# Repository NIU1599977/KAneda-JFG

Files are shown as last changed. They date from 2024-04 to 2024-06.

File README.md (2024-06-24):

# KAneda-JFG

Motocicleta auto-balanceable capaz de reconocer señales de tráfico mediante visión por computador.

## Tabla de Contenidos

+ [Descripción del Proyecto](#descripción-del-proyecto)
+ [Librerías y Configuración](#librerías-y-configuración)
+ [Componentes Electrónicos](#componentes-electrónicos)
+ [Componentes Mecánicos](#componentes-mecánicos)
+ [Esquema Eléctrico](#esquema-eléctrico)
+ [Diseño 3D](#diseño-3d)
+ [Arquitectura del Software](#arquitectura-del-software)
+ [Algorítmica](#algorítmica)
+ [Visión por Computador](#visión-por-computador)
+ [Simulación](#simulación)
+ [Contribuciones y Agradecimientos](#contribuciones-y-agradecimientos)
+ [Autoría](#autoría)
+ [Bibliografía](#bibliografía)

## Descripción del Proyecto

Este proyecto de motocicleta auto-balanceable surge con la visión de desarrollar un vehículo autónomo capaz de detectar y obedecer las señales de tráfico sin la intervención de un conductor. El propósito principal es brindar a la Dirección General de Tráfico (DGT) una herramienta para llevar a cabo demostraciones y programas educativos sobre seguridad vial. Utilizando técnicas avanzadas de visión por computador, nuestra moto puede interpretar y responder de manera precisa a las señales del entorno, lo que la convierte en un prototipo innovador en el campo de la movilidad autónoma.

La tecnología de auto-balanceo de la motocicleta se basa en el proyecto [Self-Balancing-Bike](https://github.com/remrc/Self-Balancing-Bike), realizado por [remrc](https://github.com/remrc) en Arduino.

## Librerías y Configuración

### Instalar Dependencias

1. Instalar git: `sudp apt install git`
2. Instalar gestor de librerías de python: `sudo apt install python3-pip`
3. Instalar librería smbus: `sudo apt install python3-smbus`
4. Instalar librería gpiozero: `sudo apt install python3-gpiozero`
5. Instalar librería mpu6050: `pip3 install mpu6050-raspberrypi`
6. Instalar librería numpy: `sudo apt install python3-numpy`
7. Instalar librería filterpy: `pip3 install filterpy`
8. Instalar librería openblas: `sudo apt install libopenblas-dev`
9. Instalar librería OpenCV: `sudo apt install python3-opencv`
10. Instalar librería PiCamera: `sudo apt install python3-picamera2`
11. Instalar Flask: `pip3 install flask`

\*Es posible que en ocasiones haya que añadir el parámetro `--break-system-packages` a los comandos `pip3 install <package>`.

### Activar Interfaces de Comunicación Hardware

1. Entrar en el asistente de configuración de la Raspberry: `sudo raspi-config`
2. Abrir _Interfacing Options_.
3. Activar cámara (_Enable Camera_).
4. Activar I2C.
5. Abrir _Advanced Options_.
6. Clicar _Expand Filesystem_.

### Activar el Demonio de PiGPIO

1. `sudo systemctl enable pigpiod`
2. `sudo pigpiod`

## Componentes Electrónicos

| Componente | Imagen | Componente | Imagen |
| --- | --- | --- | --- |
| [Kit Raspberry Pi Zero W + MicroSD 32GB](https://tienda.bricogeek.com/placas-raspberry-pi/1082-kit-basico-raspberry-pi-zero-wifi-microsd-32gb.html) |  | [Cámara Raspberry Pi v2 - 8 Megapíxeles](https://tienda.bricogeek.com/accesorios-raspberry-pi/822-camara-raspberry-pi-v2-8-megapixels.html) |  |
| [Cable cámara Raspberry Pi Zero (30cm)](https://tienda.bricogeek.com/accesorios-raspberry-pi/1562-cable-camara-raspberry-pi-zero-30cm.html) |  | [Módulo GY-521 Acelerómetro y Giroscopio MPU-6050](https://tienda.bricogeek.com/acelerometros/1682-modulo-gy-521-acelerometro-y-giroscopio-mpu-6050.html) |  |
| [Servo estándar S3003, 360 Grados](https://tienda.bricogeek.com/motores/118-servomotor-de-rotacion-continua-s3003-360-grados.html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) |  | [Motor paso a paso 28BYJ-48 (5V) con driver ULN2003](https://tienda.bricogeek.com/motores-paso-a-paso/969-motor-paso-a-paso-28byj-48-5v-con-driver-uln2003.html) |  |
| [Motor micro metal 75:1 HP con eje extendido](https://tienda.bricogeek.com/motores-dc/803-motor-micro-metal-751-hp-con-eje-extendido.html) |  | [BTS7960 Driver motor 43A de alta potencia](https://tienda.bricogeek.com/controladores-motores/1560-bts7960-driver-motor-43a-de-alta-potencia.html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) |  |
| [Bateria Lipo 1000mAh / 3.7V - 603050](https://tienda.bricogeek.com/baterias-lipo/135-bateria-lipo-1000mah-603050-37v.html) |  | [Cargador LiPo PowerBoost 500](https://tienda.bricogeek.com/convertidores-de-voltaje/677-cargador-lipo-powerboost-500.html) |  |

## Componentes Mecánicos

### Movimiento

| Componente | Imagen | Unidades |
| --- | --- | --- |
| [Rueda Solarbotics antideslizante](https://tienda.bricogeek.com/robotica/230-rueda-solarbotics-antideslizante.html) |  | 2 |
| [Rodamiento 608-2RS (8x22x7mm)](https://tienda.bricogeek.com/rodamientos/1294-rodamiento-608-2rs-8x22x7mm.html) |  | 2 |

### Tornillos

| Métrica | Longitud (cm) | Partes | Unidades | Tuercas |
| --- | --- | --- | --- | --- |
| M1 | 1 | Soporte Motor - Motor | 2 | Sí |
| M2 | 1 | Cámara | 2 | Sí |
| M2 | 2 | Servo | 2 | Sí |
| M3 | 1 | Soporte Stepper | 2 | Sí |
| M3 | 1,5 | Manillar, Frontal - Base, Base - Motor, Soporte Motor - Soporte Motor, Soporte Motor - Soporte Motor, Soporte Motor - Base | 12 | Sí |
| M3 | 2 | Culo | 4 | Sí |
| M3 | 3 | Base - Base | 2 | Sí |
| M4 | 0,5 | Volante de Inercia | 16 | Sí |

## Esquema Eléctrico

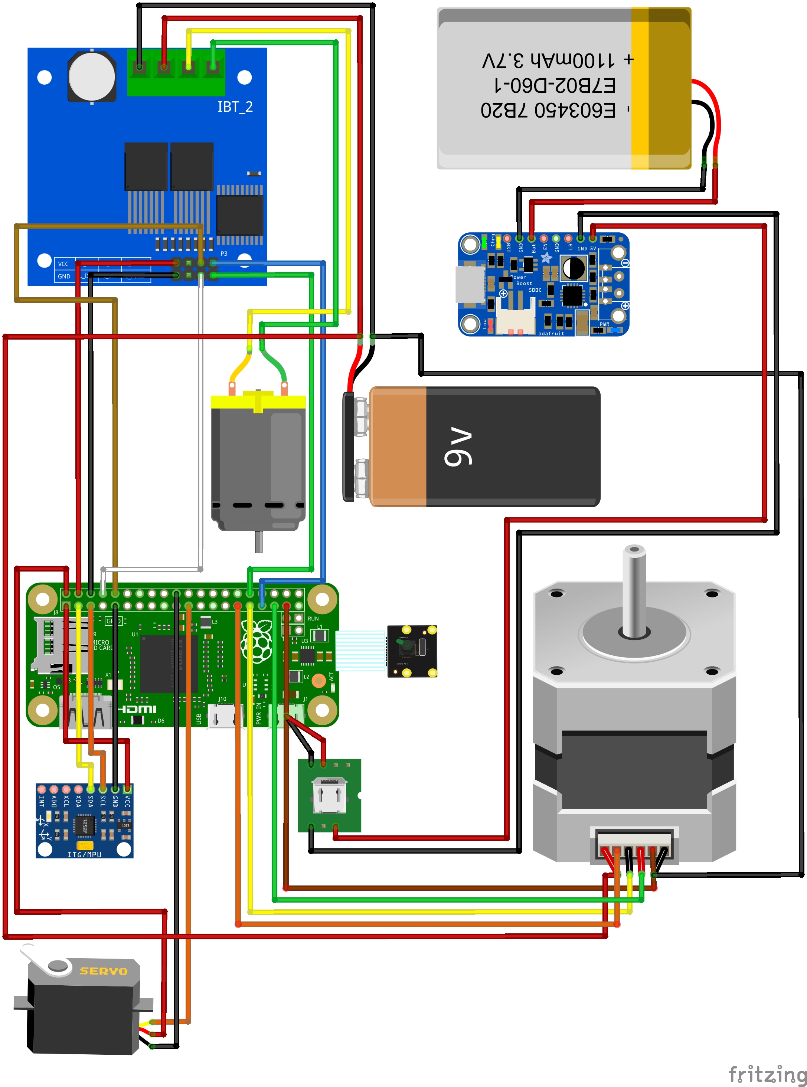
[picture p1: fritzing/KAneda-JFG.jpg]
KAneda-JFG


## Diseño 3D

Para el diseño 3D se ha optado por emplear los softwares FreeCAD y Cinema4D debido a que uno de los integrantes ya estaba familiarizado con él. El esqueleto de la motocicleta ha venido dado por el proyecto realizado por remrc, el cual tiene compartido en la página Thingiverse los [modelos](https://www.thingiverse.com/thing:5887157/files) que ha utilizado.

Estos modelos se han modificado para adecuarlos a nuestros componentes y de esta manera no exceder el presupuesto proporcionado por el profesorado. Los modelos han sido modificados de la siguiente manera.

### Manillar

Para el manillar, se ha utilizado el micro-servo SG90, por ello, ha sido necesario adaptar la pieza donde se asienta este componente.

| Antes | Después |
| --- | --- |
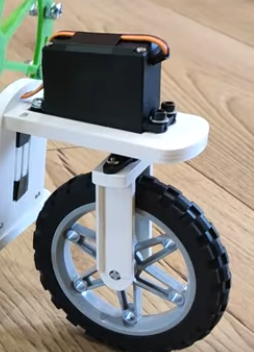
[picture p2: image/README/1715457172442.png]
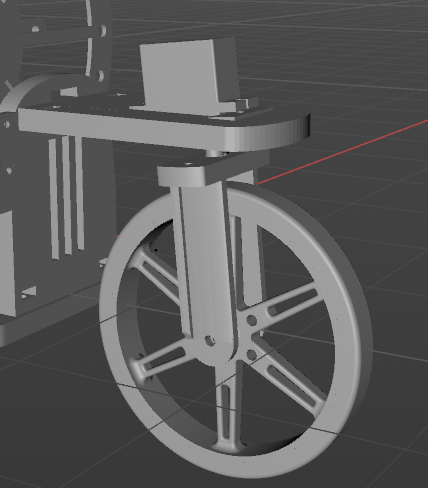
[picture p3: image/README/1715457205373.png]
|  |  |

### Volante de inercia

El volante de inercia es el alma de esta motocicleta, por tanto su diseño se ha intentado mantener con respecto al utilizado por remrc. En nuestro caso, hemos adaptado el eje de adhesión para asegurar la compatibilidad con nuestro motor pololu.

| Antes | Después |
| --- | --- |
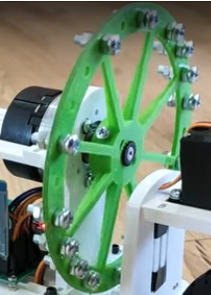
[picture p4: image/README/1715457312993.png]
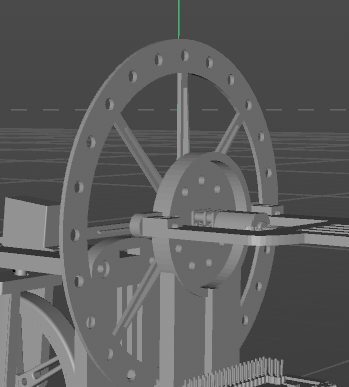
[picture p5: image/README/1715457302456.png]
|  |  |

### Cámara RPi

La motocicleta tiene soporte para utilizar visión por computador, por ello, se ha modificado la pieza que une al manillar con el cuerpo central de la motocicleta. La cámara se situaría en un lateral, esto es debido a que si se situase al frente del vehiculo, el cable no sería suficiente para llegar hasta el cuerpo central. La visión se vería ligeramente mermada a un lado por el propio manillar y la rueda delantera pero no debería suponer ningún problema.

| Antes | Después |
| --- | --- |
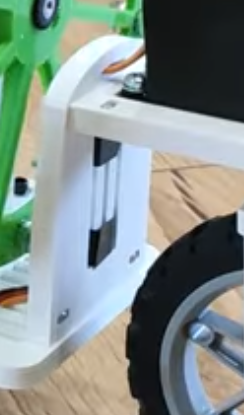
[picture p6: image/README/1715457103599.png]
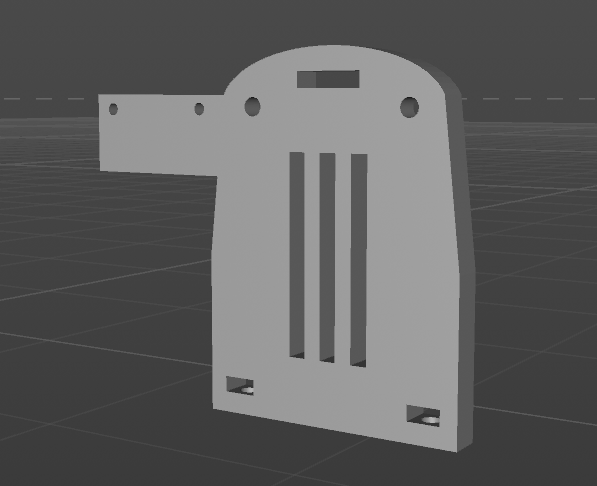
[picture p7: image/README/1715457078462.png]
|  |  |

| Visión de la cámara |
| --- |
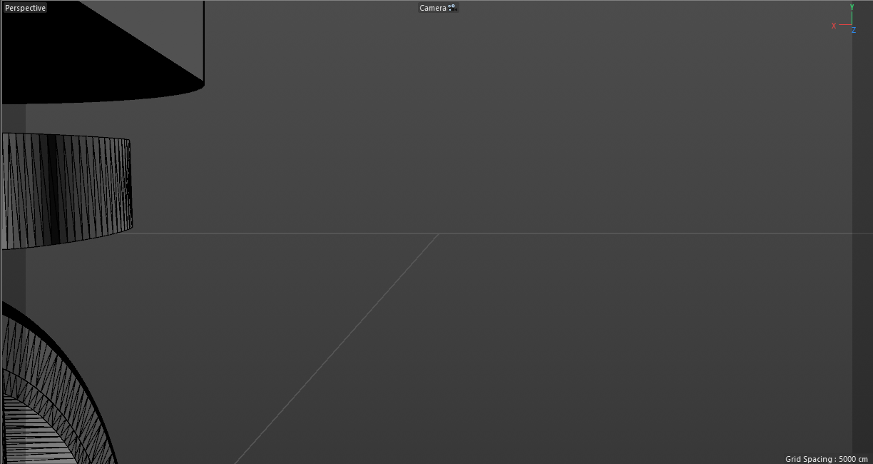
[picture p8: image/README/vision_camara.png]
camera_vision
|  |

### Parte posterior

La parte posterior de la motocicleta ha sido completamente rediseñada desde cero debido al límite presupuestario. En un principio remrc utilizaba un stepper y una correa para transmitir la potencia a la rueda trasera, nosotros hemos optado por utilizar un micro-stepper y transmitir la potencia mediante el uso de dos engranajes de 16 dientes, disponibles en [thingiverse](https://www.thingiverse.com/thing:146289). Además, hemos optado por añadir un rodamiento de 22mm x 8mm para mitigar las imprecisiones que puedan surgir utilizando un eje transversal e impresión 3D. Finalmente añadir que como eje se ha utilizado un tornillo M3 de 15 mm, de esta manera la rueda y uno de los engranajes de 16 dientes girarán solidariamente y podrá recibir la potencia del micro-stepper. Con ello, nuestra parte trasera quedaría tal que así.

| Antes | Después |
| --- | --- |
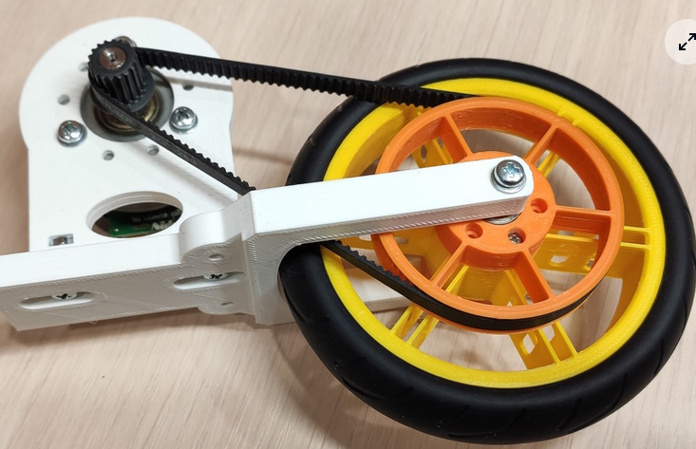
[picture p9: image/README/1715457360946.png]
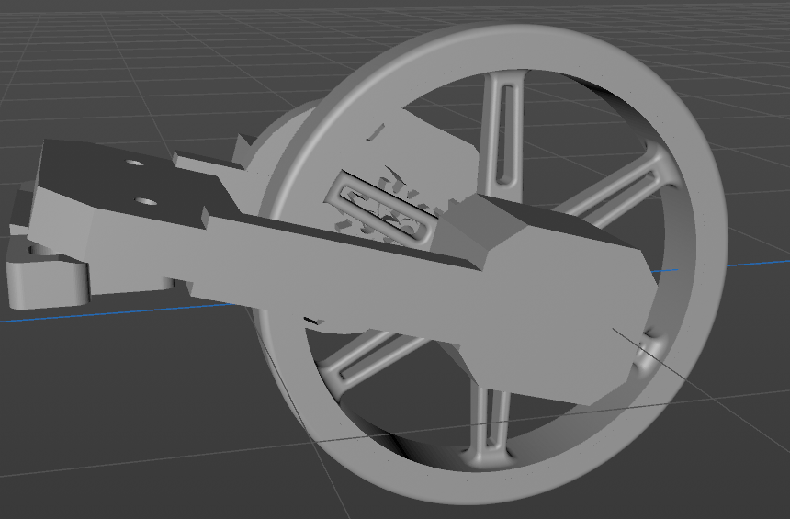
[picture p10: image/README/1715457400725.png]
|  |  |

## Arquitectura del Software

En relación con el componente de software de nuestro proyecto, hemos emprendido la tarea de traducir e interpretar el código del proyecto de referencia, que originalmente fue diseñado para Arduino (código **.ino**). Sin embargo, la principal complejidad de nuestro robot radica en que no estamos utilizando Arduino, sino una Raspberry Pi Zero. Como resultado, hemos tenido que investigar exhaustivamente sobre las librerías adecuadas para nuestra placa y además adaptar su código y reestructurarlo (e incluso añadir funcionalidades) en base a nuestro proyecto.

El software de Kaneda-JFG se compone de cuatro módulos, los cuales, en su totalidad, habilitarán la funcionalidad completa del robot.

### Módulo de Detección de señales
Este módulo, tal y como indica su nombre se centra en la detección de la señales de tráfico y la reacción del robot a cada una de estas. 

### Módulo de control de la inclinación
El módulo de control de inclinación de la moto se ejecuta mediante un bucle que constantemente utiliza el **Filtro de Kalman** para predecir en aproximadamente 1 segundo, la inclinación que tendrá la moto.

De esta forma, al conocer la próxima inclinación del robot se podrá contrarrestar utilizando el volante de inercia para mantener la moto en pie en todo momento.

### Módulo de control de la moto
Otro módulo importante de la moto, es el módulo que nos permite controlar la moto. A la vez que este va prediciendo su inclinación con el filtro de kalman (módulo de control de la inclinación) también espera comandos que el usuario debe introducir.

El usuario debe introducir una serie de comandos para indicar el camino que debe recorrer la moto, indicando en todo momento la distancia a recorrer y el ángulo (si tiene que ir recto o girar).

**Ejemplo:**
>> 20,0 0,90 5,0 0,45 35,0 0,0 (ve recto 20cm, gira 90º derecha, ve recto 5cm, gira 45º derecha, ve recto 35cm y para).

### Módulo de Interacción HW/SW
Este es de los módulos más importante del programa que controla la moto, ya que es el que permite la comunicación entre la parte física de la moto con la parte Software de esta.

Junta cada una de las funcionalidades que ofrece la moto y las coordina según los datos que envíen los sensores de la moto, los comandos introducidos por el usuario, etc.

## Algorítmica

### Filtro de Kalman

Para poder controlar la orientación de la moto y evitar que se caiga, hemos pensado en implementar el famoso algoritmo conocido como **Filtro de Kalman**.

#### Breve descripción del filtro de Kalman

El filtro de Kalman se trata de un algoritmo que puede estimar parámetros observables y no observables con gran precisión en tiempo real. Es utilizado para estimar las variables de un sistema basándose en medidas con ruido, calcula las diferentes probabilidades del estado de un sistema. Lo podemos ver como una caja negra, donde las entradas son ruidosas y, a veces, contienen mediciones inexactas. Y los resultados son menos ruidosos y tienen más precisión.

Este algoritmo es muy utilizado en robótica y sistemas en tiempo real que necesitan información confiable. Su importancia recae en poder estimar parámetros del sistema que no se pueden medir u observar con precisión, permitiendo así a los sistemas tener un mayor control y, por tanto, más capacidades.

Este algoritmo se basa principalmente en 2 pasos:

1) **Predicción:** Donde, basándose en el estado anterior del sistema se predice el estado actual del sistema y su incertidumbre.
2) **Actualización (o Corrección):** Se utilizan las mediciones actuales para actualizar la estimación del estado y reducir la incertidumbre (el ruido). 

Estos 2 pasos se repiten en cada paso de tiempo para producir una estimación del estado de forma más precisa.

#### ¿Cómo encaja con nuestro proyecto?

Precisamente, por lo explicado en el subapartado anterior, el filtro de Kalman se trata de una herramienta poderosa que nos permitirá obtener la futura inclinación que tomará la moto antes de que ocurra.
De esta manera, sabiendo este dato, nos permitirá corregir la inclinación de la moto ajustando los parámetros del volante de inercia (ajustando potencia y dirección) según la inclinación de la moto.

## Visión por Computador
### Breve descripción de la idea de visión por computador
La implementación que queremos hacer, va sobre poner una camará en la moto, para que cuando vea una señal, poder reaccionar a ella dependiendo del significado de la señal.
### YOLO
Yolo es la tecnologia que usaremos para nuestra implementación para el tema de la visión por computador. Yolo se refiere a "You Only Look Once", un algoritmo de detección de objetos en tiempo real. Desarrollado por Joseph Redmon, YOLO es conocido por su rapidez y precisión al identificar y localizar objetos en imágenes y videos en una sola pasada por la red neuronal, lo que lo hace muy eficiente para aplicaciones en tiempo real como la vigilancia, la conducción autónoma y la robótica. Este algoritmo ha sido recomendado para el profesor de prácticas de Visión por Computador.
### Ejemplos del algoritmo Yolo
| Ejemplo 1 | Ejemplo 2 |
| --- | --- |
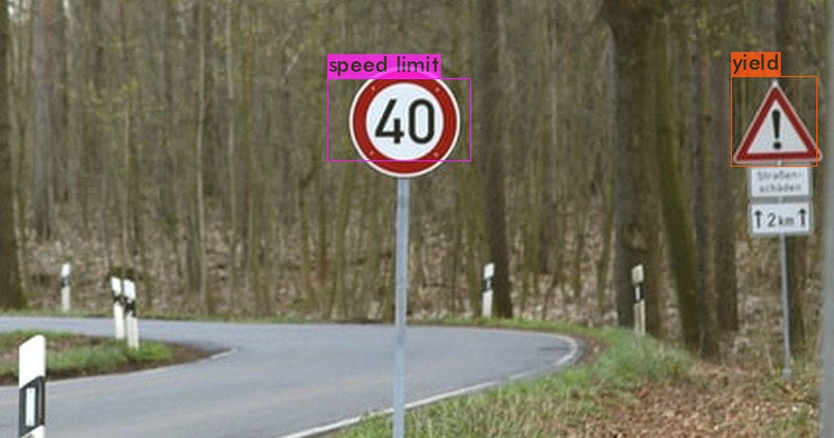
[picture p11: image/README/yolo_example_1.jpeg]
yolo_example_1
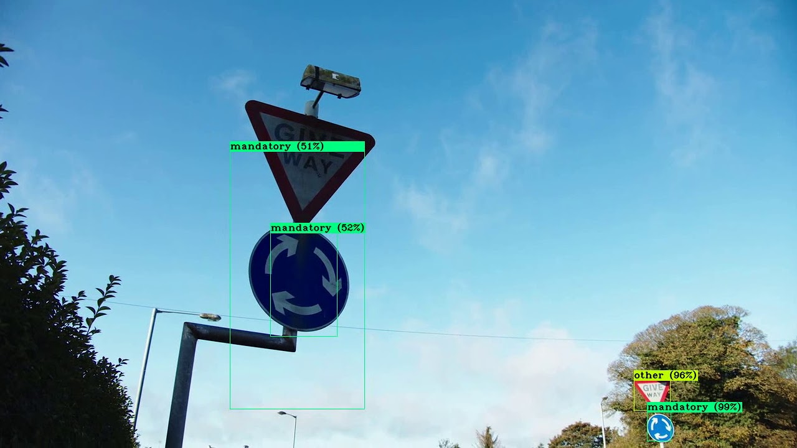
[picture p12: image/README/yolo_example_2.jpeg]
yolo_example_2
|  |  |

### TensorFlow Lite
TensorFlow Lite es una versión ligera y optimizada de TensorFlow, diseñada específicamente para permitir el despliegue de modelos de aprendizaje automático en dispositivos con recursos limitados, como teléfonos móviles, microcontroladores y otros dispositivos integrados. Esta tecnología es especialmente relevante para proyectos de visión por computador donde la eficiencia y la velocidad son críticas, y los recursos de hardware son limitados.

### Teachable Machine
Teachable Machine es una herramienta interactiva y accesible creada por Google, diseñada para permitir a cualquier persona, sin necesidad de conocimientos avanzados en programación o aprendizaje automático, entrenar modelos de inteligencia artificial (IA). Esta plataforma simplifica el proceso de creación de modelos de aprendizaje automático mediante una interfaz fácil de usar, que permite a los usuarios crear modelos personalizados para tareas de clasificación de imágenes, sonidos y poses corporales.


### Aplicación en la KAneda-JFG

**Captura de Imagen:** La moto está equipada con una cámara de la raspberry pi que capturará imagenes en tiempo real.

**Procesamiento de Imagen:** Las imagenes capturadas se pasan al algoritmo YOLO, que detecta y clasifica las señales de tráfico presentes en la imagen.

**Identificación de Señales** YOLO puede detectar diversas señales de tráfico como "Stop", "Límite de Velocidad", "Ceda el Paso", "No Estacionar", entre otras.

**Reacción de la Moto** Dependiendo de la señal detectada, la moto tomará diferentes acciones. 

**El ejemplo que queremos aplicar:**

**Señal de Stop:** La moto reducirá la velocidad y se detendrá completamente.

**Límite de Velocidad:** La moto ajustará su velocidad para cumplir con el límite indicado.

**Ceda el Paso:** La moto reducirá la velocidad y esperará hasta que sea seguro avanzar.

## Simulación
La siguiente  [Simulacion](https://uab-my.sharepoint.com/personal/1522975_uab_cat/_layouts/15/stream.aspx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) muestra el comportamiento idóneo que debería tener nuestro robot.

## Contribuciones y Agradecimientos

Queremos dar un agradecimiento a todo el profesorado de Robòtica, Llenguatge i Programació por la ayuda ofrecida y el seguimiento en nuestro proyecto KAneda-JFG para que saliera adelante.

## Autoría

| Nombre | NIU | Cargo |
| --- | --- | --- |
| Francesc Gallego Palomo | 1467414 | Responsable de Visión por Computador |
| Göran Hatero Comino | 1600920 | Responsable de Software |
| Aleix Valdivieso González | 1522975 | Responsable de Diseño 3D |
| Jordi Pradas López | 1599977 | Responsable de Hardware |

## Bibliografía
[Cross-Compiling Tensorflow Lite](https://www.tensorflow.org/lite/guide/build_cmake_arm?hl=es)

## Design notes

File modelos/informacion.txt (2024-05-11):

./bike/central/volante_inercia.stl imprimirlo en metal

Todo el resto de piezas en plástico

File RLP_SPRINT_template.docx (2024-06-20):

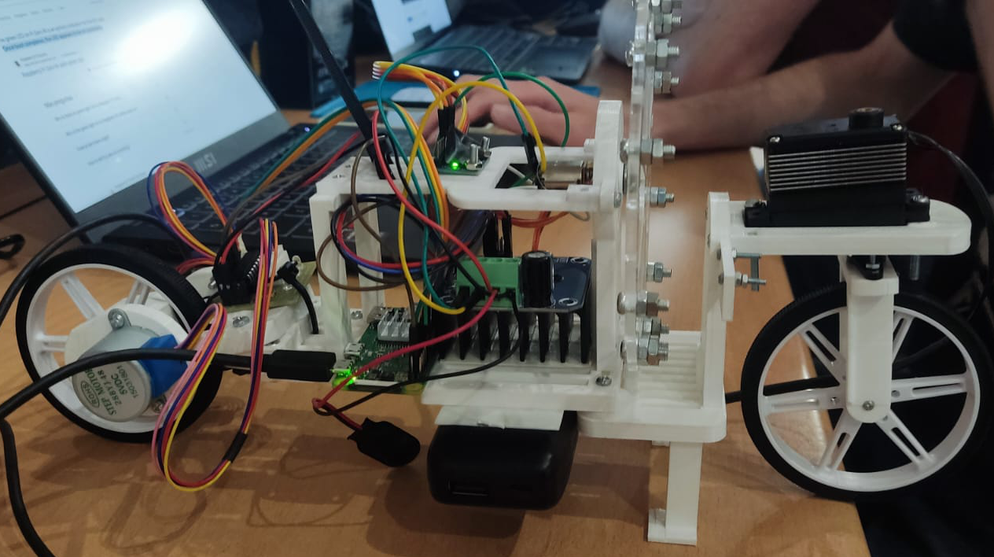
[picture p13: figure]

# Kaneda-JFG

Motocicleta autoequilibrante capaz de realizar un circuito con señales de tráfico.

PROJECT SPRINT #2.
DATE: 26 de Junio de 2024

Göran Hatero Comino 1600920
Jordi Pradas López 1599977
Aleix Valdivieso Gonzalez 1522975
Francesc Gallego Palomo 1467414

Kaneda-JFG

Motocicleta autoequilibrante capaz de realizar un circuito con señales de tráfico.

# Descripción del proyecto

Este proyecto de motocicleta auto-balanceable surge con la visión de desarrollar un vehículo autónomo capaz de detectar y obedecer las señales de tráfico sin la intervención de un conductor. El propósito principal es brindar a la Dirección General de Tráfico (DGT) una herramienta para llevar a cabo demostraciones y programas educativos sobre seguridad vial. Utilizando técnicas avanzadas de visión por computador, nuestra moto puede interpretar y responder de manera precisa a las señales del entorno, lo que la convierte en un prototipo innovador en el campo de la movilidad autónoma.

Pero la principal característica atractiva de esta motocicleta es su capacidad de autoequilibrarse mediante un volante de inercia y los datos proporcionados por el giroscopio.

# Componentes electrónicos

Los componentes electrónicos de la moto son los siguientes:

- Raspberry Pi Zero Wifi + MicroSD 32GB
- Cable Cámara Raspbery Pi Zero
- Módulo GY-521 Acelerómetro y Giroscopio MPU-6050 (https://tienda.bricogeek.com/acelerometros/1682-modulo-gy-521-acelerometro-y-giroscopio-mpu-6050.html)
- Micro servo miniatura SG90 (https://tienda.bricogeek.com/servomotores/968-micro-servo-miniatura-sg90.html)
- Stepper GM15BY
- Módulo de controlador de Motor BTS7960
- Motor paso a paso 28BYJ-48 (5V) con driver ULN2003 (https://tienda.bricogeek.com/motores-paso-a-paso/969-motor-paso-a-paso-28byj-48-5v-con-driver-uln2003.html)
- Batería RoHS 6700mAh 5V
- Motor Micro Metal LP con reductora 10:1 (https://tienda.bricogeek.com/motores/113-motor-micro-metal-lp-con-reductora-10-1.html)

# Esquema

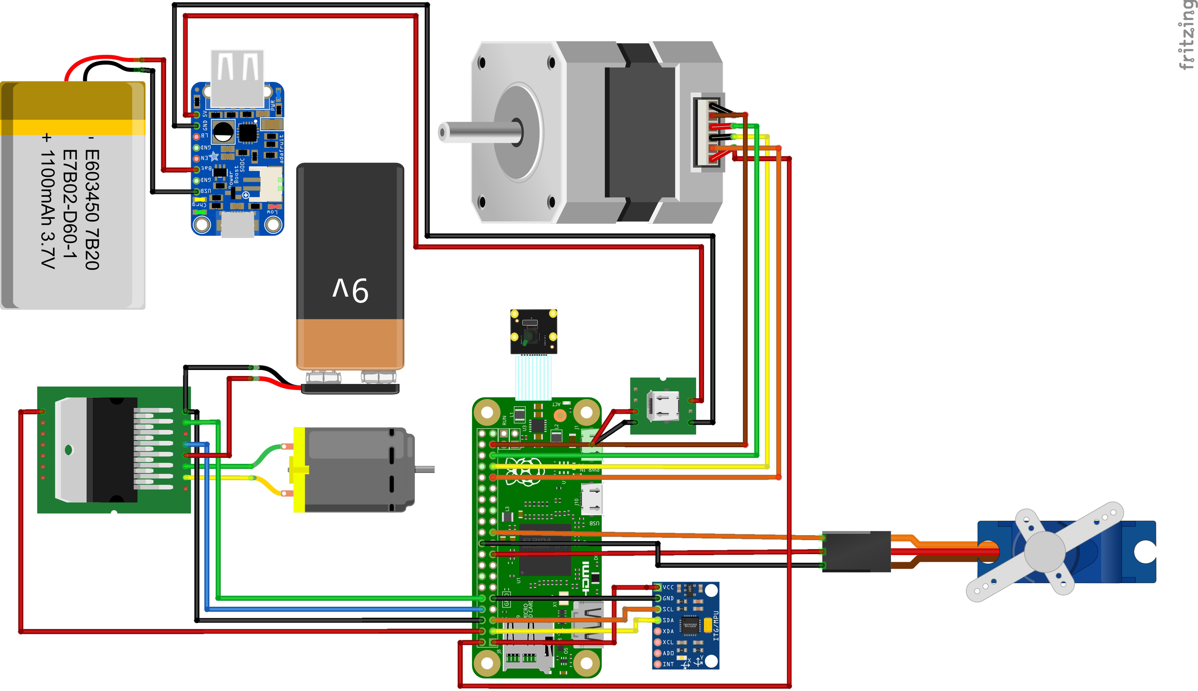
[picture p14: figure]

Acelerómetro MPU_6050

- VCC → 3v3 – Pin 1
- GND → GND – Pin 9
- SCL → I2C1 SCL – GPIO 3 – Pin 5
- SDA → I2C1 SDA – GPIO 2 – Pin 3

Servo motor TowerPro SG90:

- VCC → 3v3 – Pin 17
- GND → GND – Pin 20
- GPIO → GPIO 9 – Pin 21

Stepper 28BYJ-48:

- VCC → 5V – Pin 2
- GND → GND – Pin 39
- IN1 → GPIO 6 – Pin 31
- IN2 → GPIO 13 – Pin 33
- IN3 → GPIO 19 – Pin 35
- IN4 → GPIO 26 – Pin 37

IBT_2 Motor Driver:

- ENL → GPIO 14 – Pin 8
- ENR → GPIO 15 – Pin 10
- RPWM → GPIO 18 – Pin 12
- LPWM → GPIO 12 – Pin 32
- 5V → 5V – Pin 4
- GND → GND – Pin 6
- B- → GND – 9V (-)
- B+ → 9V (+)
- M+ → Motor (+)
- M- → Motor (-)

# Componentes extras y piezas 3D

- Manillar
- Volante de inercia
- Estructura Cámara RPi
- Parte Posterior
- Rueda Solarbotics antideslizante
- Rodamiento 608-2RS (8x22x7mm)

MANILLAR

Para el manillar, se ha utilizado el micro-servo SG90, por ello, ha sido necesario adaptar la pieza donde se asienta este componente.


VOLANTE DE INERCIA

El volante de inercia es el alma de esta motocicleta, por tanto, su diseño se ha intentado mantener con respecto al utilizado por remrc. En nuestro caso, hemos adaptado el eje de adhesión para asegurar la compatibilidad con nuestro motor pololu.


ESTRUCTURA CÁMARA RPi

La motocicleta tiene soporte para visión por computador, con una cámara montada en un lateral debido a la longitud limitada del cable. Aunque la visión puede estar ligeramente obstruida por el manillar y la rueda delantera, no debería representar un problema significativo.


PARTE POSTERIOR

La parte posterior de la motocicleta ha sido rediseñada por completo debido a limitaciones presupuestarias. Se ha reemplazado el sistema original de stepper y correa de remrc por un micro-stepper con dos engranajes de 16 dientes encontrados en Thingiverse. Además, se ha añadido un rodamiento de 22mm x 8mm para mejorar la precisión utilizando un eje transversal e impresión 3D. Un tornillo M3 de 15mm se usa como eje, permitiendo que la rueda y un engranaje giren conjuntamente y reciban la potencia del micro-stepper.


RUEDA ANTIDESLIZANTE

Las ruedas antideslizantes destán diseñadas para proporcionar tracción superior y estabilidad en diversas superficies. Son ideales para proyectos de robótica, como nuestra motocicleta autobalanceable, ya que su diseño robusto y su material de alta fricción aseguran un agarre eficiente, mejorando el control y la maniobrabilidad del vehículo. Estas ruedas son duraderas y pueden manejar el desgaste, lo que las hace adecuadas para aplicaciones exigentes.

Risk # | Description | Probability (High/Medium/Low) | Impact (High/Medium/Low) | Contingency plan
1 | Que la rueda delantera vibre y por lo tanto, desestabilice al robot | Alto | Medio | Poner un servo de mayor Calidad.
2 | Que los engranajes no sean solidarios entre ellos | Baja | Alto | Apretar los engranajes y no mover la moto manualmente con las manos.
3 | Que falle el giroscopio | Baja | Alto | Implementación de try-except en el Código.

# Riesgos previstos y plan de contingencia

Referencias

This project has been inspired by the following Internet projects:

https://www.youtube.com/watch?v=Je9Y2WaRB6g&ab_channel=ReM-RC

(https://www.youtube.com/watch?v=Je9Y2WaRB6g&ab_channel=ReM-RC)https://www.youtube.com/watch?v=SUVtObDFFWY&ab_channel=IRIMLABKOREATECH

Kaneda-JFG

Kaneda-JFG 3

Kaneda-JFG 1

RPL – Computer Engineering. UAB (Barcelona) 2023-2024

Sprint #2 Date: 26 Junio 2024

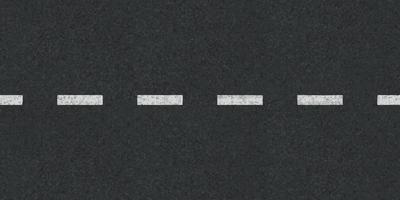
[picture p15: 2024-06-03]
simulation/resources/road-highway-with-dotted-line-top-view-background-free-vector.jpg

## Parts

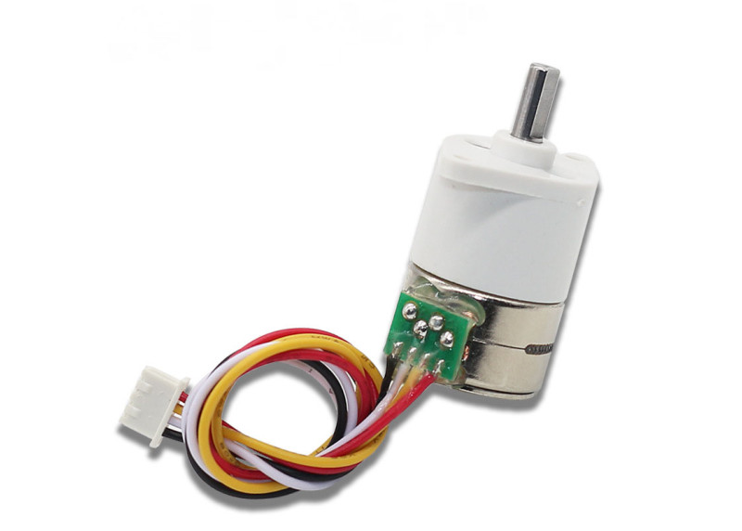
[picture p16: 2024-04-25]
fritzing/Componentes/micromotor-stepper-gm15by-15mm-5v-1150.jpg

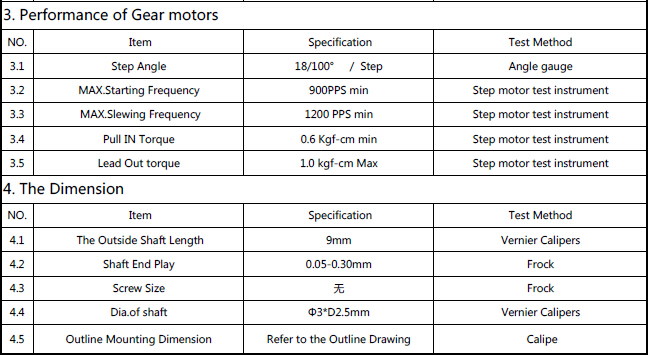
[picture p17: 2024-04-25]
fritzing/Componentes/GM15BY.jpg

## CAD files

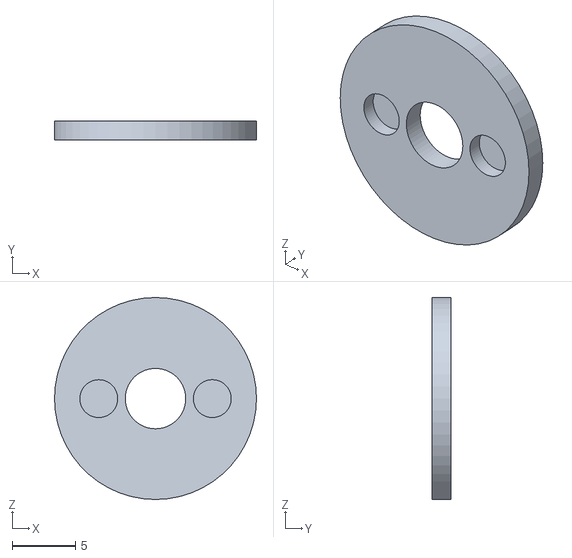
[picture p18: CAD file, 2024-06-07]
modelos/bike/central/espaciador.stl
16.0 x 1.50 x 16.0

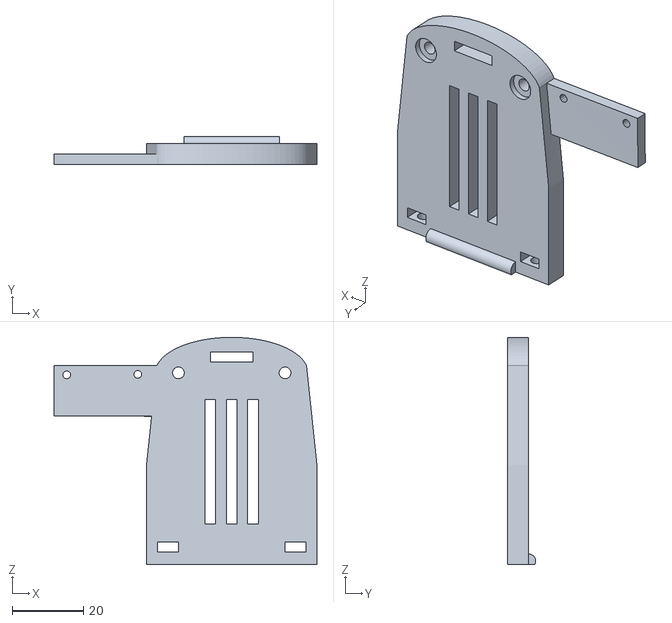
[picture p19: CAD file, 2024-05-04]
modelos/bike/frontal/frontal_vertical.stl
74.0 x 8.02 x 64.0

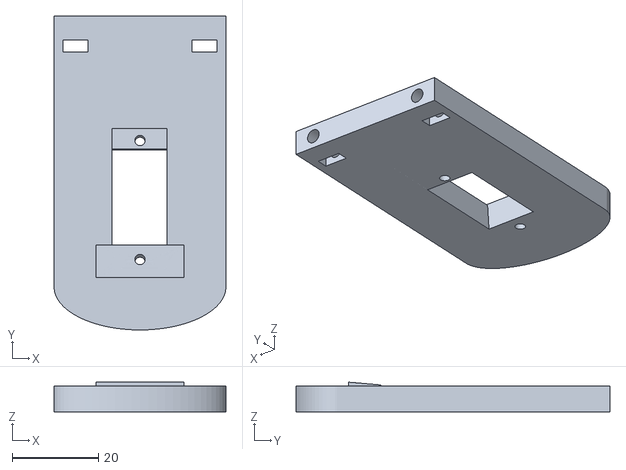
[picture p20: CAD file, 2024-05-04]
modelos/bike/frontal/manillar/supp_superior.stl
40.0 x 73.0 x 6.92

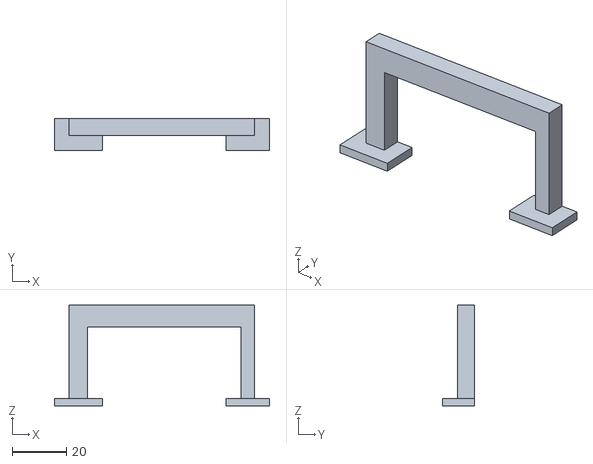
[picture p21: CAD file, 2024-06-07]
modelos/bike/pata_cabra.stl
79.0 x 11.8 x 37.0

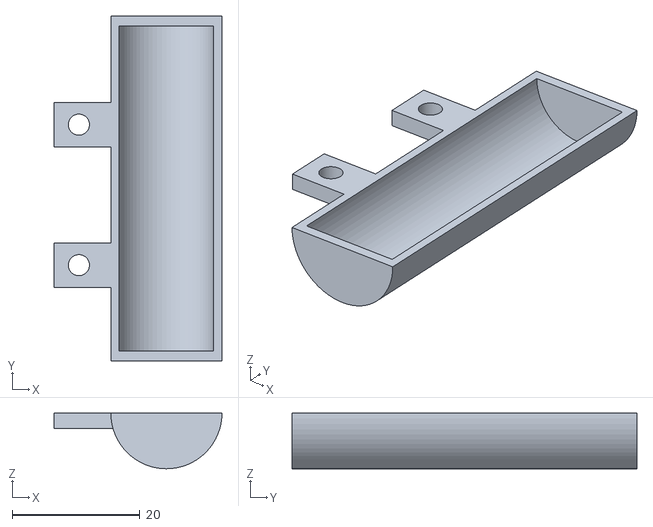
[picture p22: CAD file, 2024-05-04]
modelos/bike/pesos/rw_bike_weight2_2x.stl
26.3 x 54.0 x 8.70

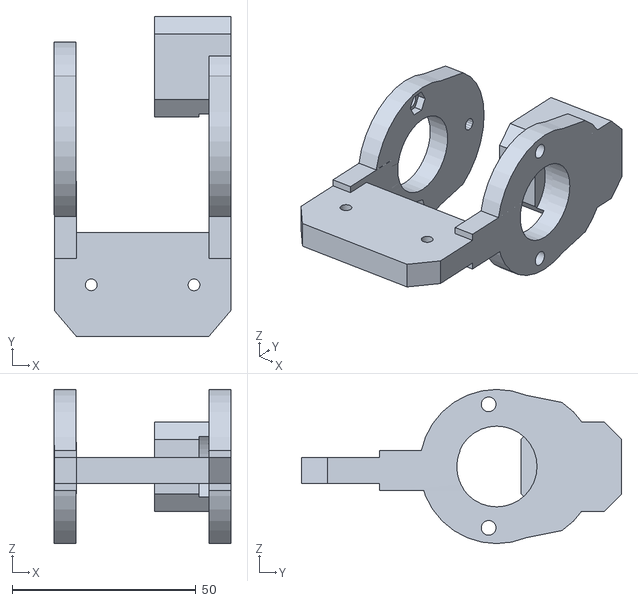
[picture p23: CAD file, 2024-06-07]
modelos/bike/trasera/pieza_trasera+contra_peso.stl
48.1 x 87.2 x 42.0

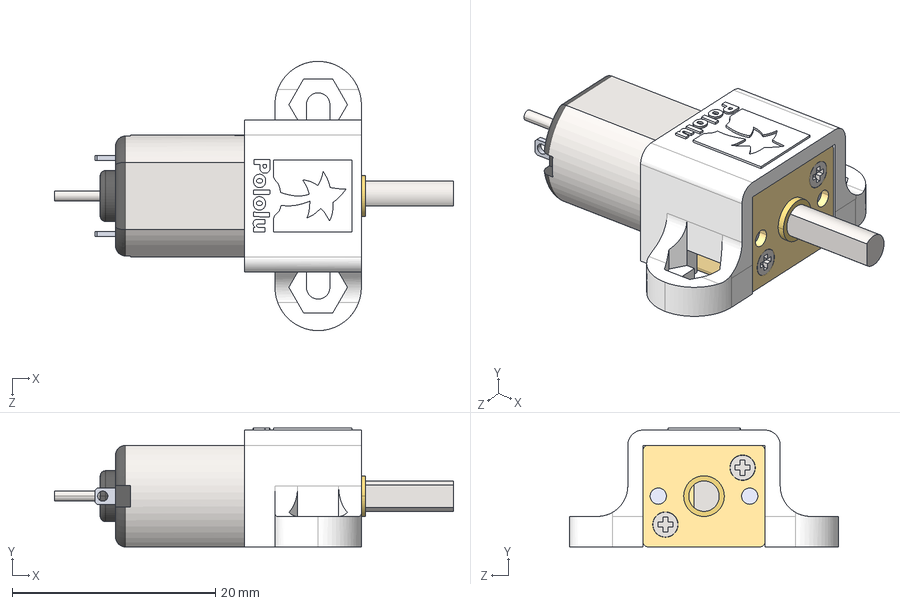
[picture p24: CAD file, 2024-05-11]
modelos/design/componentes_freecad/Pololu Micro Metal Gearmotor 3D (STEP) Models/With Bracket/mmgm-pm-ext-shaft-with-1086-bracket.step
39.3 x 11.7 x 26.5 mm

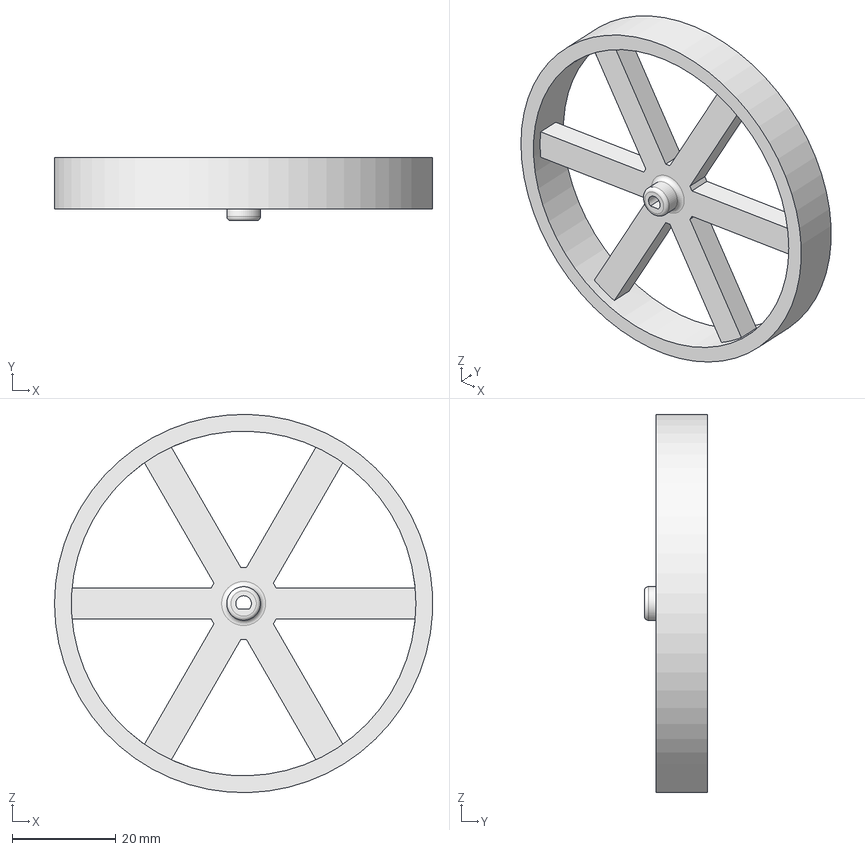
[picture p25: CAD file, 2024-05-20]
modelos/design/componentes_freecad/rueda_2.FCStd
72.9 x 12.3 x 73.0 mm

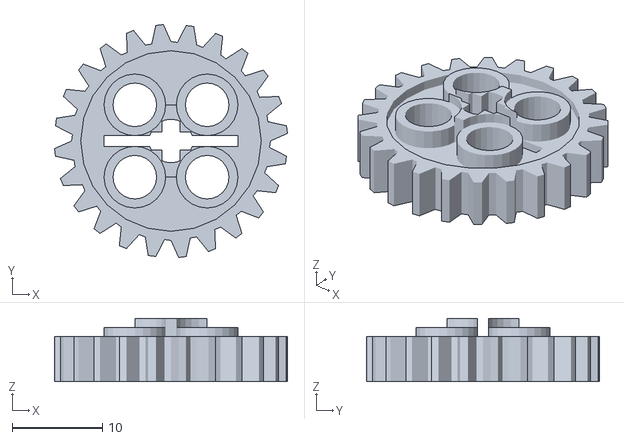
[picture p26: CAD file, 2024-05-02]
modelos/design/engranajes/bbStock24TGear.stl
25.8 x 25.8 x 7.00

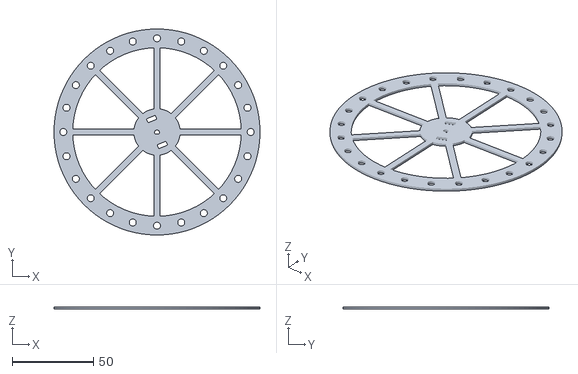
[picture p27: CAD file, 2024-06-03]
modelos/design/inericia.stl
126.4 x 126.4 x 1.48

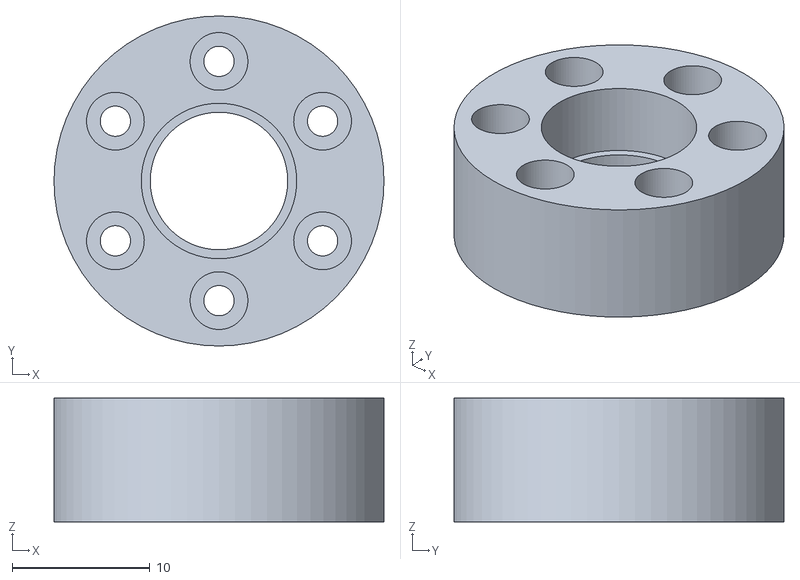
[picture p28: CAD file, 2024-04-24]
modelos/design/original_parts/rw_bike_rear_wheel_bearing_holder_1x.stl
24.0 x 24.0 x 9.00

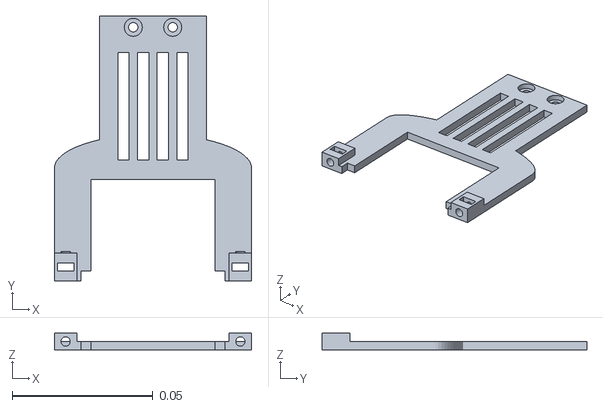
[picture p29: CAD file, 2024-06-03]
modelos/soporte_motoro2.stl
0.07 x 0.094 x 0.006

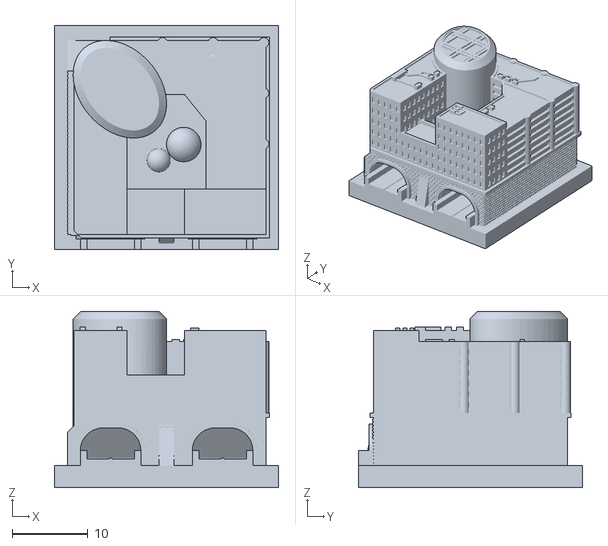
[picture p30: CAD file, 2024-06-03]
simulation/resources/greeble_tunnel housing_hollowcube_fr.STL
29.6 x 29.6 x 23.3

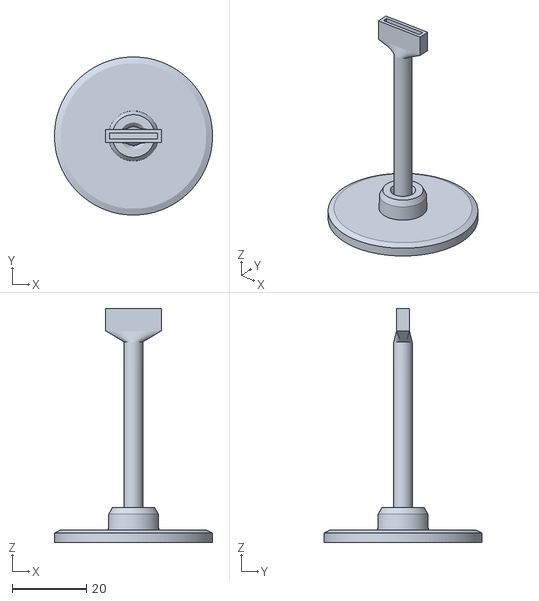
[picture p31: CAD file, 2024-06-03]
simulation/resources/stop-sign-coloradomaker/cuerpo.stl
42.5 x 42.5 x 62.9

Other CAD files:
modelos/design/componentes/rueda-Fusion.stl
modelos/bike/central/centrador_2.stl
modelos/bike/frontal/manillar/rw_bike_front_fork_1x.stl
modelos/bike/pesos/rw_bike_weight1_2x.stl
modelos/bike/central/centrador.stl
modelos/bike/central/rw_bike_body1_1x.stl
modelos/bike/central/rw_bike_body2_1x.stl
modelos/bike/central/rw_bike_frame1_1x.stl
modelos/bike/central/rw_bike_frame2_1x.stl
modelos/bike/central/soporte_motor.stl
modelos/bike/central/volante_inercia.stl
modelos/bike/frontal/manillar/espaciador_delantero.stl
modelos/bike/trasera/centrador.stl
modelos/bike/trasera/gear-stepper.stl
modelos/bike/trasera/gear_rueda.stl
modelos/bike/trasera/pieza_trasera.stl
modelos/bike/trasera/rw_bike_rear_fork_holder_1x.stl
modelos/bike/trasera/soporte_stepper.stl
modelos/design/componentes/camara.stl
modelos/design/componentes/rueda.stl
modelos/design/componentes/servo.stl
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

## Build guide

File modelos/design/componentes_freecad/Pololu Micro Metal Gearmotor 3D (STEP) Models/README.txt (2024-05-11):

Pololu Micro Metal Gearmotor 3D (STEP) Models

File name key:

pm = precious metal brushes (LP, MP, and HP versions)
cb = carbon brushes (HPCB versions)

1000 = 1000:1 gear ratio, which has a longer gearboxes than the other gear ratios

enc-back-con = Encoder with Back Connector version
enc-side-con = Encoder with Side Connector version
ext-shaft = Extended Motor Shaft version

with-1086-bracket = gearmotor shown with Pololu item #1086 bracket (https://www.pololu.com/product/1086) and also covers #989 bracket which is the same but black (https://www.pololu.com/product/989)
with-1089-ext-bracket = gearmotor shown with Pololu item #1089 bracket (https://www.pololu.com/product/1089)

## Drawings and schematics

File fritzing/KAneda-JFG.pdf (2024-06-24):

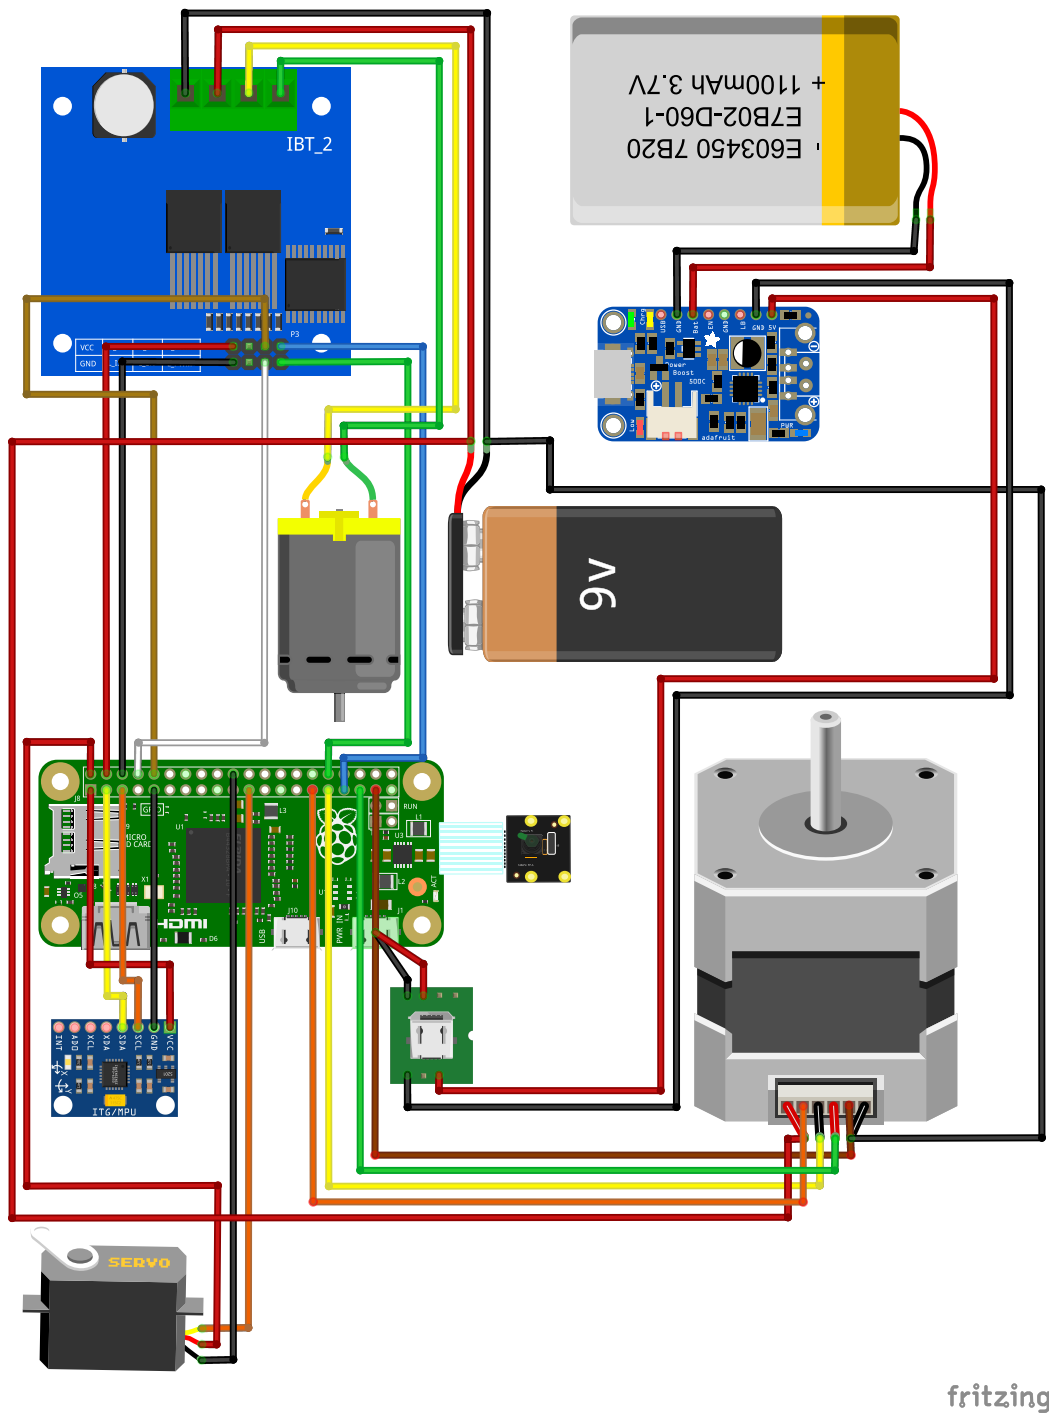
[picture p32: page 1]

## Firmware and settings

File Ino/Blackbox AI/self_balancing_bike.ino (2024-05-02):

#include <Wire.h>
#include <EEPROM.h>
#include <ServoTimer2.h>

#define PWM_1         9
#define DIR_1         7
#define PWM_2         10
#define DIR_2         5 

#define ENC_1         2
#define ENC_2         3

#define BRAKE         8
#define BUZZER        12
#define VBAT          A7

#define STEERING_MAX    350
#define SPEED_MAX       80
#define STEERING_CENTER 1500
#define ST_LIMIT        5
#define SPEED_LIMIT     4

float Gyro_amount = 0.996;  

bool vertical = false;
bool calibrating = false;
bool calibrated = false;

float K1 = 115;
float K2 = 15.00;
float K3 = 8.00;
float K4 = 0.60;
float loop_time = 10;

struct OffsetsObj {
  int ID;
  int16_t AcY;
  int16_t AcZ;
};
OffsetsObj offsets;

float alpha = 0.4; 

int16_t  AcY, AcZ, GyX, gyroX, gyroXfilt;

int16_t  AcYc, AcZc;
int16_t  GyX_offset = 0;
int32_t  GyX_offset_sum = 0;

float robot_angle;
float Acc_angle;

volatile byte pos;
volatile int motor_counter = 0, enc_count = 0;
int16_t motor_speed;
int32_t motor_pos;
int steering_remote = 0, speed_remote = 0, speed_value = 0, steering_value = STEERING_CENTER;;

int bat_divider = 58; // this value needs to be adjusted to measure the battery voltage correctly

long currentT, previousT_1, previousT_2 = 0;  

ServoTimer2 steering_servo;

/*
  Esta función se ejecuta una vez cuando el programa comienza. 
  Se inicializan los pines de entrada y salida, se configuran los motores y el servo, y se leen los valores de calibración de la EEPROM.
*/
void setup() {
  Serial.begin(115200);

  // Pins D9 and D10 - 7.8 kHz
  TCCR1A = 0b00000001; 
  TCCR1B = 0b00001010; 

  steering_servo.attach(A3); 
  steering_servo.write(STEERING_CENTER); 

  pinMode(DIR_1, OUTPUT);  
  pinMode(DIR_2, OUTPUT);
  pinMode(BRAKE, OUTPUT);
  pinMode(BUZZER, OUTPUT);
  pinMode(ENC_1, INPUT);
  pinMode(ENC_2, INPUT);
  
  Motor1_control(0);
  Motor2_control(0);

  attachInterrupt(0, ENC_READ, CHANGE);
  attachInterrupt(1, ENC_READ, CHANGE);

  EEPROM.get(0, offsets);
  if (offsets.ID == 35) calibrated = true;
    else calibrated = false;
  delay(3000);
  beep();
  angle_setup();
}

/*
  Esta es la función principal que se ejecuta continuamente. En cada iteración, se leen los parámetros de control, se calcula el ángulo del robot, se actualiza la velocidad del motor y se controlan los motores y el servo en función de estos valores.
  Si el robot está en posición vertical, calibrado y no se está calibrando, se activa el freno, se calcula la velocidad del giroscopio, se actualiza la posición del motor y se controlan los motores y el servo.
  Si el robot no está en posición vertical, se desactiva el freno, se centra el servo y se detienen los motores.
*/
void loop() {

  currentT = millis();

  if (currentT - previousT_1 >= loop_time) {
    //Tuning();  
    readControlParameters();  
    angle_calc();

    motor_speed = -enc_count;
    enc_count = 0;

    if (vertical && calibrated && !calibrating) {
      digitalWrite(BRAKE, HIGH);
      gyroX = GyX / 131.0; // Convert to deg/s

      gyroXfilt = alpha * gyroX + (1 - alpha) * gyroXfilt;

      motor_pos += motor_speed;
      motor_pos = constrain(motor_pos, -110, 110);
      
      int pwm = constrain(K1 * robot_angle + K2 * gyroXfilt + K3 * motor_speed + K4 * motor_pos, -255, 255); 
      Motor1_control(-pwm);

      if ((speed_value - speed_remote) > SPEED_LIMIT)
        speed_value -= SPEED_LIMIT;
      else if ((speed_value - speed_remote) < -SPEED_LIMIT)
        speed_value += SPEED_LIMIT;
      else
        speed_value = speed_remote;  
      
      if ((steering_value - STEERING_CENTER - steering_remote) > ST_LIMIT)
        steering_value -= ST_LIMIT;
      else if ((steering_value - STEERING_CENTER - steering_remote) < -ST_LIMIT)
        steering_value += ST_LIMIT;
      else
        steering_value = STEERING_CENTER + steering_remote;

      steering_servo.write(steering_value);
      Motor2_control(speed_value);
    } else { 
      digitalWrite(BRAKE, LOW);
      steering_value = STEERING_CENTER;
      steering_servo.write(STEERING_CENTER);
      speed_value = 0;
      Motor1_control(0);
      Motor2_control(0);
      motor_pos = 0;
    }
    previousT_1 = currentT;
  }
  
  if (currentT - previousT_2 >= 2000) {    
    battVoltage((double)analogRead(VBAT) / bat_divider); 
    if (!calibrated && !calibrating) {
      Serial.println("first you need to calibrate the balancing point...");
    }
    previousT_2 = currentT;
  }
}

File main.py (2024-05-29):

import hardware.imu
from hardware.servo import *
from hardware.stepper import *
import threading

def main():
    s1 = Stepper([31,33,35,37])
    
    turn_value = [-1, 0, 1]
    for i in range(2):
        t1 = threading.Thread(target=turn, args=(turn_value[i],))
        t2 = threading.Thread(target=s1.move, args=(512,0.00059,))
    
        t1.start()
        t2.start()

        t1.join()
        t2.join()


if __name__ == '__main__':
    main()

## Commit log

2024-04-17 added components cad
    [bateria.FCStd, camara.FCStd, giroscopio.FCStd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]
2024-04-24 ref models
    [rw_bike_bearing_center_2x.stl, rw_bike_body1_1x.stl, rw_bike_body2_1x.stl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]
2024-04-24 stepper ok
2024-04-24 renamed folders
    [bateria.FCStd, camara.FCStd, giroscopio.FCStd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]
2024-04-24 added stl electric components
    [camara.stl, rueda.stl, servo.stl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]
2024-04-24 fusioned freecad part models
    [rueda.FCStd, stepper_board.FCStd]
2024-04-25 Fritzing
    Componentes y esquema eléctrico, representado con protoboard.
    [KAneda-JFGbb.fzz]
2024-05-02 diseño 0.7
    [bbStock16TGear.stl, bbStock24TGear.stl, bbStock40TGear.stl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]
2024-05-04 bike 0.7
    [bateria.FCStd, bbStock16TGear.stl, bbStock24TGear.stl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]
2024-05-06 Refactor 1
    [KAneda-JFGbb.fzz]
2024-05-11 compatible con rodamiento
    [centrador.stl, montura_trasera.stl, pieza_trasera.stl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]
2024-05-11 Add datasheets and schematics
2024-05-12 Update README.md
    Creación subapartados Arquitectura del Software y explicación filtro de kalman
2024-05-20 added new flywheel, and designs
    [rueda-Fusion.stl, rueda_2.FCStd, volante_inercia.stl]
2024-05-21 Kalman filter
2024-05-22 Update Fritzing Schema
    [KAneda-JFG.fzz]
2024-05-27 Update Fritizing Schema
    [KAneda-JFG.fzz, KAneda-JFGbb.fzz]
2024-05-27 changed gear wheel design. better fit
    [gear_rueda.stl]
2024-05-29 added test for new motor controller
2024-06-07 Limpieza de código
2024-06-07 new models
    [centrador_2.stl, espaciador.stl, pata_cabra.stl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]
2024-06-07 pata de cabra
    [pata_cabra.stl]
2024-06-10 refactor de todo un poco
2024-06-10 primera aguantada & servo cambiado para que no pete
2024-06-12 Add calibrate to remrc_balancing.py
2024-06-13 Add s3003 servo datasheet
2024-06-14 Preparación de jupyter con todas las librerias necesarias + prueba de velocidad de joint
2024-06-15 reorganización
    [Stop Sign v1.stl, cuerpo.stl, greeble_tunnel housing_hollowcube_fr.STL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]
2024-06-21 filterpy kalman implementado
2024-06-21 quitado print dc
2024-06-21 parece que da buenos resultados. pero el dt=0.
2024-06-21 los angulos los mide bien (si no gira muy rapido), la velocidad angular da casi 0... habria que configurar a mano el mpu6050 para asegurarnos que trabaja en el rango correcto
    [kalman_test.py, moto.py]
2024-06-21 añadido filtro complementario para el angulo
2024-06-21 dt se pasa por parametro e intento de ajuste de las variables
2024-06-21 bajar el maximo dc a 30
2024-06-24 Update Fritzing and libraries
    [KAneda-JFG.fzz]
2024-06-24 Update Fritzing (Sí, otra vez)
    [KAneda-JFG.fzz]
2024-06-24 unitary camera
